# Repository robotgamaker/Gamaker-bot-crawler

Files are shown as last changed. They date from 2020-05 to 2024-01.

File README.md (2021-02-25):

# Gamaker-bot-crawler
Código arduino , STLs y app para crear un pequeño robot cuadrúpedo muy ágil, con capacidad para superar obstáculos
Hay que imprimir dos veces el archivo PARpatasPistoriusV5.stl (hasta tener dos pares de patas) y 
también hay que imprimir dos veces el archivo "ChasisFinal_GamakerBot4.stl"  .
Con los dos chasis se monta un "sandwich" sujeto por 4 tornillos de métrica 3 de 20 mm de longitud (3x20).
La bateria va entre las dos planchas y los 4 miniservos. En el piso "superior " va la electrónica.

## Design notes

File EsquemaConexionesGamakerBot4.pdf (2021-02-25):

Conexiones del GamakerBot4:

A0(14): -> Tx de placa Bluetooth (BT)

A1(15): ->Rx de placa BT

A4: -> zumbador

D2: -> servo delantero derecho (hombro derecho)

D3: -> servo delantero izdo (hombro izdo)

D4: -> servo trasero derecho (cadera derecha)

D5: -> servo trasero izquierdo (cadera izda)

D6: -> servo giratorio cabeza

D8: -> LED rojo

D9: -> LED amarillo

D10:-> LED verde

D12: -> sensor ultrasónico, pin Echo

D13: -> sensor ultrasónico, pin Trigger

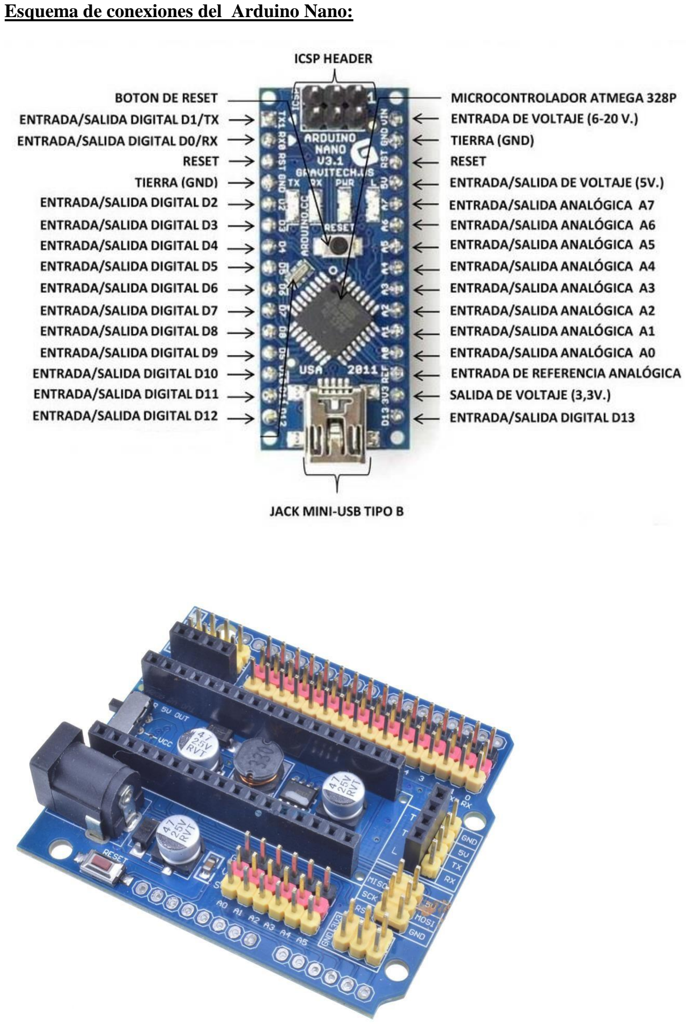
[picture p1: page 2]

Esquema de conexiones del Arduino Nano:

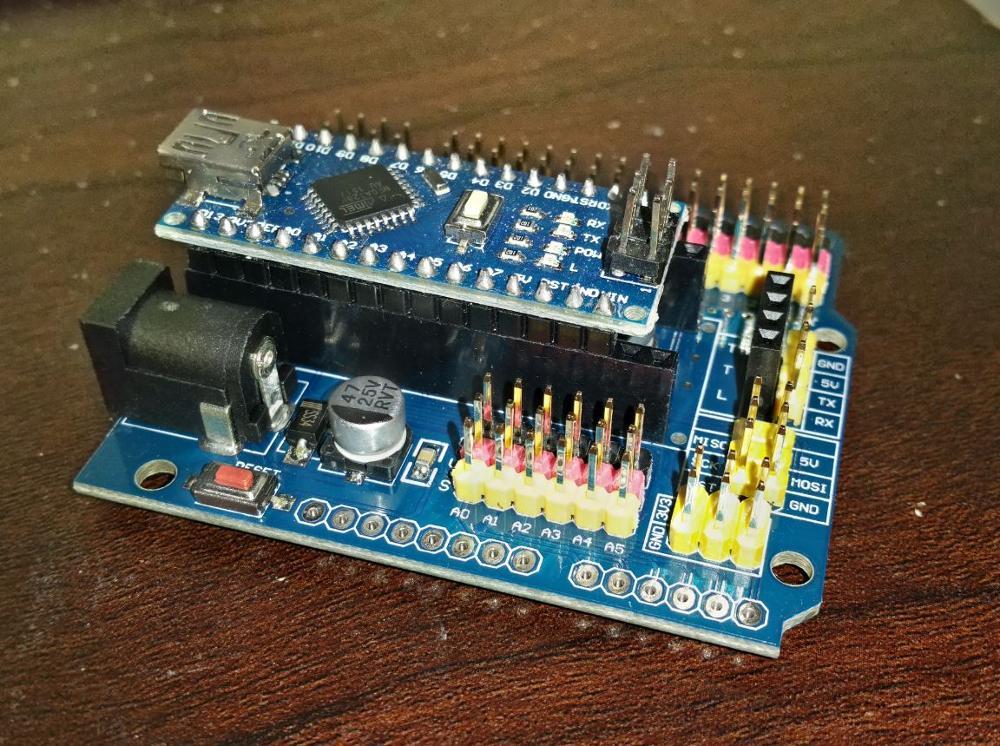
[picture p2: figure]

Distribución de teclas en la app Cheetah :

G | F | I
g | f | i
L | l | S | r | R
H | b | j
H | B | J
U | V | W
X | Y | Z

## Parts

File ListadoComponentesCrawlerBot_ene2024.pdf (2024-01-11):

Listado de componentes del robot CrawlerBot : www.3dsolid.es

Presupuesto con precios del 11/01/2024:

Miniservos (8 +2 de repuesto: 21,41€/10unids) de rotación continua (360 grados), de engranajes metálicos (los de nylon se rompen muy rápido, no comprar!): https://es.aliexpress.com/item/1005004550692203.html

Batería Lipo, 1 + repuestos, (3,7V, 1000 mA aprox ) se carga hasta 4,2 V y se conecta a GND y 5V del arduino Nano, pedir el modelo con conector blanco X5C, para luego poder recargarlo con el siguiente componente que pediremos OJO!): 7,43€:2/u

https://es.aliexpress.com/item/4001305039983.html

Cable de carga de la batería Lipo (se conecta por USB a nuestro cargador de móvil estándar: de 5V, 1A): 1,57€/unid

https://es.aliexpress.com/item/4001023158270.html

Modulos BlueTooth (slave: de 4 pines), para controlar el robot desde nuestro móvil Android con la app Cheetah (tb disponible en este gitHub) : 5,15€/2unids https://es.aliexpress.com/item/4000830084058.html

Arduino Nano: 6,98€/2 unids https://es.aliexpress.com/item/32647196840.html?spm=a2g0s.9042311.0.0.39da63c0 ATthIT (https://es.aliexpress.com/item/32647196840.html?spm=a2g0s.9042311.0.0.39da63c0ATthIT)

Tornillos de 2,5 mm de diámetro y 14 mm de largo para atornillar bien las patas al eje metálico de los servos: 2,28€/bolsa 50 unids https://es.aliexpress.com/item/32835829915.html?spm=a2g0s.9042311.0.0.3d2f63c0kaEIxs

Tornillos de 3 mm de diámetro y 20 mm de largo, para unir las dos placas de plástico del chásis : de venta en ferreterías y grandes almacenes, por ejemplo, Leroy Merlin. 2 €/bolsa

Cables de conexión de arduino de 10 cm de longitud: Hembra-hembra : 2,63 €/2 pack https://es.aliexpress.com/item/4000439969887.html

Voltímetro , para controlar el voltaje de la batería y no descargarla por debajo de los 3,7 V (se carga hasta los 4,2 V) : 2,18€/ 2 unids https://es.aliexpress.com/item/32901073658.html

Un mini-interruptor de encendido/apagado del bot: 0,97/10 unids https://es.aliexpress.com/item/4001165826718.html

- Como app de control bluetooth se puede usar la que tb se adjunta en el github (Cheetah):
https://github.com/robotgamaker/Gamaker-bot-crawler

O también “Arduino Bluetooth RC Car controller”(se aconseja tener instaladas las dos) :
https://play.google.com/store/apps/details?id=braulio.calle.bluetoothRCcontroller&hl=es_419 (https://play.google.com/store/apps/details?id=braulio.calle.bluetoothRCcontroller&hl=es_419)

-Shield para Arduino Nano: 6,56 € /2 unids https://es.aliexpress.com/item/1859164365.html

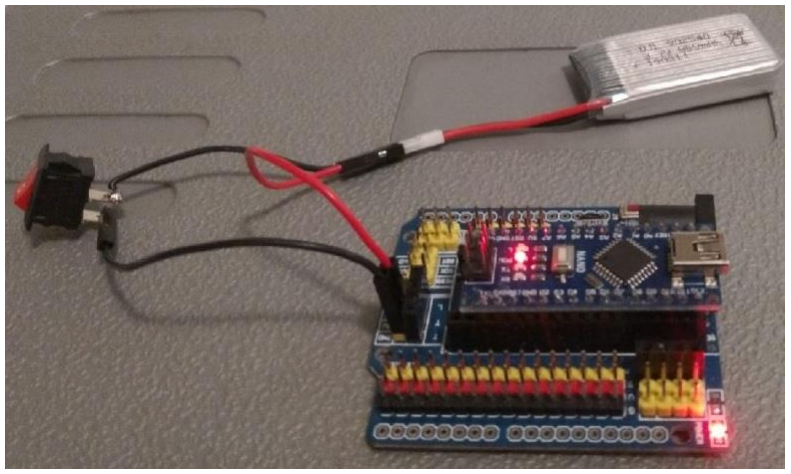
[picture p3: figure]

Link a zumbadores pasivos: 1,56€/2 unids https://es.aliexpress.com/item/32809816924.html

Link a sensor ultrasónico (detector obstáculos): 1,90€/2 unids https://es.aliexpress.com/item/4000899658467.html

Link a “semáforo led RGB” : 2,15 €/2 unids https://es.aliexpress.com/item/1005003926496876.html

1 miniservo 940D (0-180º) para girar la cabeza (8,51 €/2 unids): https://es.aliexpress.com/item/4000459542063.html

Ejemplo de presupuesto para hacer 2 crawlerBots con componentes de aliexpress:

1. 10 servos de engranaje metalico 360º(+ envio en todos) | 21,41€
2. 2 baterias Lipo 3,7 V, 1000 mA : | 7,50
3. 4 cables de carga de de batería (2 por robot) : | 6,15
4. 2 modulos Bluetooth hc-06 (4 pins) : | 4,68
5. 2 placas controladoras Arduino nano con cable: | 6,98
6. 1 bolsas de tornillos 2,5 x 14 mm: | 2,54
7. 1 bolsas de tornillos 3 x 20 mm en Leroy Merlin: | 2
8. 2 bolsitas de cables female-female: | 2,63
9. 2 minivoltimetros para controlar el voltaje de la batería: | 2,18
10. Kit de 10 mininteruptores: | 0,97
11. 2 shields para conectar el nano, la alimentación y los motores 6,56
12. 2 zumbadores pasivos (para que emita sonido/melodías) | 1,56
13. 2 sensores ultrasónicos (detectores de obstáculos): | 1,90
14. 2 semaforos leds , Rojo, Verde, Amarillo | 2,15
15. 2 miniservos 0-180º MG90D : | 8,51
16. 2 Cajas grande (bazar) de plástico transp para guardar todo....... 5
TOTAL: | 82,72
Cada pareja de crawlerBot costaría 82,72/2= 41,36 aprox (los precios pueden variar)
*Precios del 11/01/2024

By Marcos Sánchez

Contacto : markrehab@hotmail.com

https://youtu.be/afSSLWHGoCMhttps://youtu.be/Y1tGxN8LFB4

http://www.3dsolid.es

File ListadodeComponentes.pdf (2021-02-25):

Listado de componentes del robot Gamaker-bot 4 Crawler :

Miniservos (4 + repuestos) de rotación continua (360 grados), de engranajes metálicos (los de nylon se rompen muy rápido, no comprar!): https://es.aliexpress.com/item/32950372601.html?spm=a2g0o.cart.0.0.57dc3c00khVMC8&mp=1 (https://es.aliexpress.com/item/32950372601.html?spm=a2g0o.cart.0.0.57dc3c00khVMC8&mp=1)

Un miniservo estándar 0-180º:

https://es.aliexpress.com/item/4000933394404.html?spm=a2g0o.cart.0.0.259b3c00zS4MK5&mp=1

Batería Lipo, 1 + repuestos, (3,7V, 1000 mA aprox ) se carga hasta 4,2 V y se conecta a GND y 5V del arduino Nano, pedir el modelo con conector blanco X5C, para luego poder recargarlo con el siguiente componente que pediremos OJO!):

https://es.aliexpress.com/item/4001127625537.html?spm=a2g0s.9042311.0.0.274263c0nBTT 4L (https://es.aliexpress.com/item/4001127625537.html?spm=a2g0s.9042311.0.0.274263c0nBTT4L)

Cable de carga de la batería Lipo (se conecta por USB a nuestro cargador de móvil estándar: de 5V, 1A):

https://es.aliexpress.com/item/32969002546.html?spm=a2g0s.9042311.0.0.677063c0Q2Q8M b (https://es.aliexpress.com/item/32969002546.html?spm=a2g0s.9042311.0.0.677063c0Q2Q8Mb)

Modulos BlueTooth (slave: de 4 pines), para controlar el robot desde nuestro móvil Android con la app Cheetah (tb disponible en este gitHub) : https://es.aliexpress.com/item/32632724017.html?spm=a2g0o.cart.0.0.11ad3c00Q6e6XO&mp=1 (https://es.aliexpress.com/item/32632724017.html?spm=a2g0o.cart.0.0.11ad3c00Q6e6XO&mp=1)

Arduino Nano:
https://es.aliexpress.com/item/32647196840.html?spm=a2g0s.9042311.0.0.39da63c0 ATthIT (https://es.aliexpress.com/item/32647196840.html?spm=a2g0s.9042311.0.0.39da63c0ATthIT)

Tornillos de 2,5 mm de diámetro y 14 mm de largo para atornillar bien las patas al eje metálico de los servos:
https://es.aliexpress.com/item/32835829915.html?spm=a2g0s.9042311.0.0.3d2f63c0kaEIxs

Tornillos de 3 mm de diámetro y 20 mm de largo, para unir las dos placas de plástico del chásis : de venta en ferreterías y grandes almacenes, por ejemplo, Leroy Merlin.

Cables de conexión de arduino de 10 cm de longitud: Macho-Hembra, y hembra-hembra :

https://es.aliexpress.com/item/4000439969887.html?spm=a2g0s.9042311.0.0.274263c0t1IvQ W (https://es.aliexpress.com/item/4000439969887.html?spm=a2g0s.9042311.0.0.274263c0t1IvQW)

Voltímetro , para controlar el voltaje de la batería y no descargarla por debajo de los 3,7 V (se carga hasta los 4,2 V) : https://es.aliexpress.com/item/32825671226.html?spm=a2g0s.9042311.0.0.274263c0WNp1 M5 (https://es.aliexpress.com/item/32825671226.html?spm=a2g0s.9042311.0.0.274263c0WNp1M5)

Un mini-interruptor de encendido/apagado del bot: https://es.aliexpress.com/item/32832762868.html?spm=a2g0o.cart.0.0.e6c13c00k5ehAD&mp=1

- Como app de control bluetooth se puede usar la que tb se adjunta en el github (Cheetah)
O también “Arduino Bluetooth RC Car controller”: https://play.google.com/store/apps/details?id=braulio.calle.bluetoothRCcontroller&hl=es_419 (https://play.google.com/store/apps/details?id=braulio.calle.bluetoothRCcontroller&hl=es_419)
- La placa de conexiones de alimentación la haremos manualmente con el soldador y un trocito rectángular de PCB.

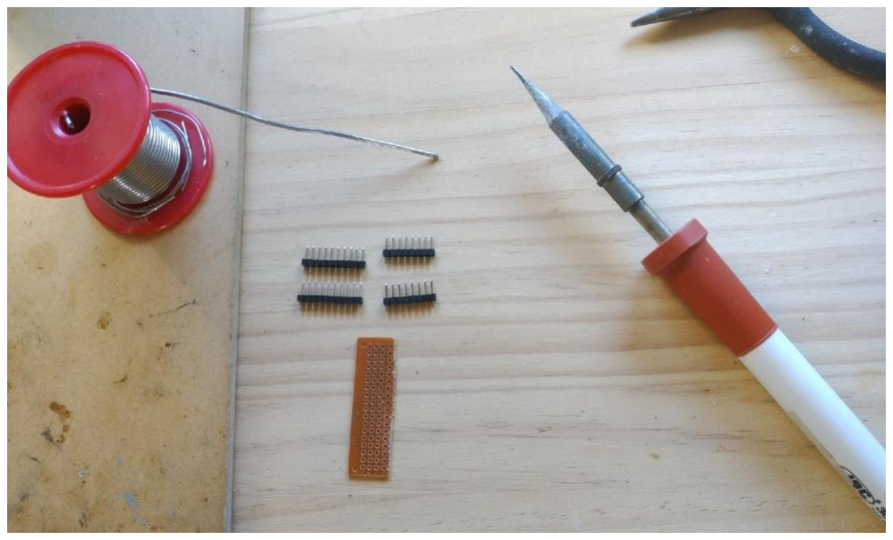
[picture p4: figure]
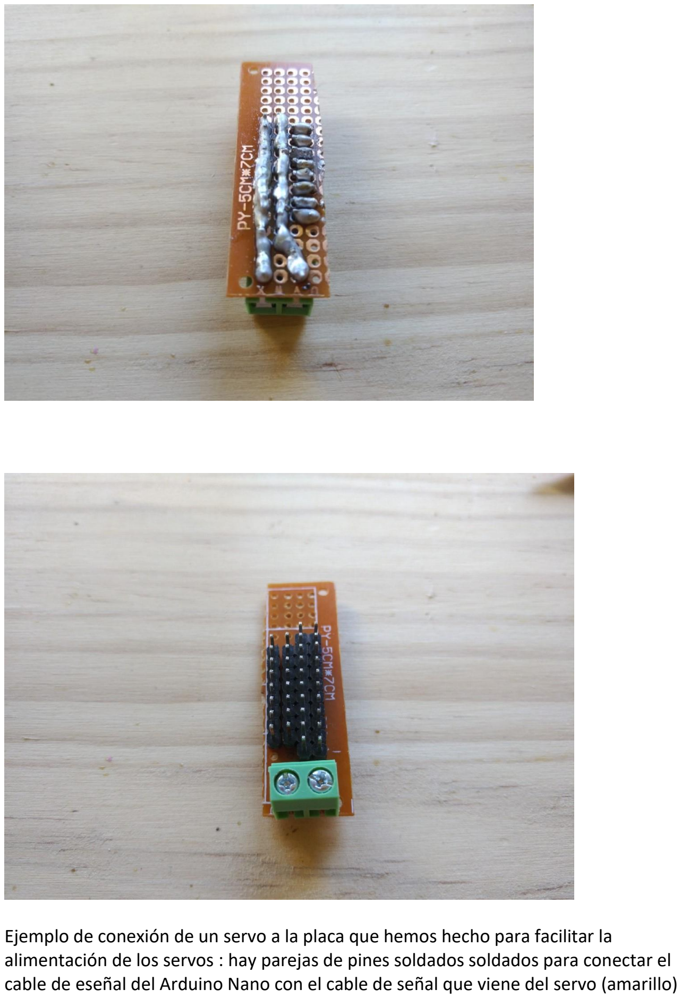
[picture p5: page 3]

Ejemplo de conexión de un servo a la placa que hemos hecho para facilitar la alimentación de los servos : hay parejas de pines soldados soldados para conectar el cable de eseñal del Arduino Nano con el cable de señal que viene del servo (amarillo)

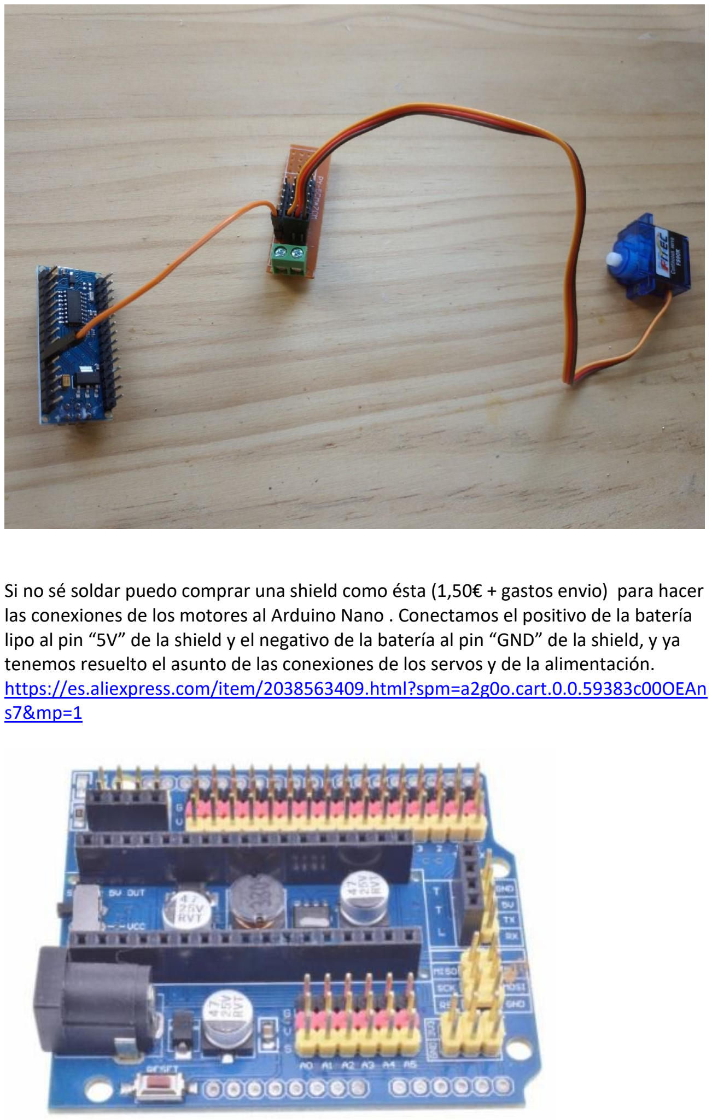
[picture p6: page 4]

Si no sé soldar puedo comprar una shield como ésta (1,50€ + gastos envio) para hacer las conexiones de los motores al Arduino Nano . Conectamos el positivo de la batería lipo al pin “5V” de la shield y el negativo de la batería al pin “GND” de la shield, y ya tenemos resuelto el asunto de las conexiones de los servos y de la alimentación. https://es.aliexpress.com/item/2038563409.html?spm=a2g0o.cart.0.0.59383c00OEAns7&mp=1 (https://es.aliexpress.com/item/2038563409.html?spm=a2g0o.cart.0.0.59383c00OEAns7&mp=1)

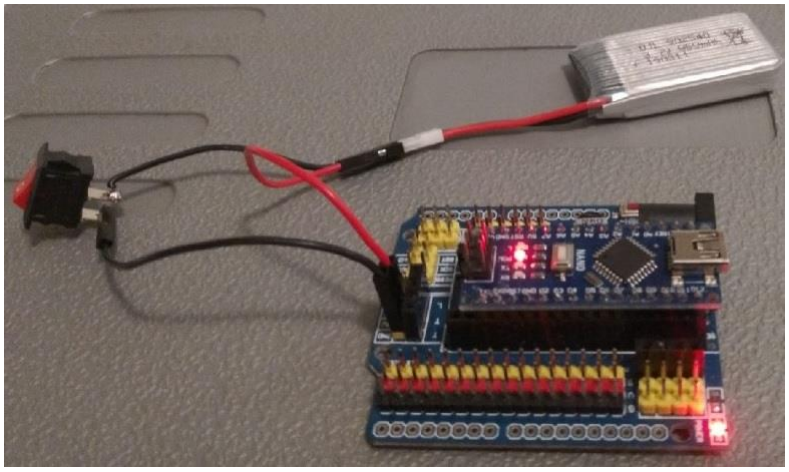
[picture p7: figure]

Ejemplo de presupuesto para hacer 2 gamakerBots4 con componentes de aliexpress:
1. 10 servos de engranaje metalico (+ envio en todos) | 14,37 €
2. 2 miniservos MG-90D (0-180º) | 5,57
3. 2 baterias Lipo 3,7 V, 1000 mA : | 6,55
4. 4 cables de carga de de batería (2 por robot) : | 2,56
5. 2 modulos Bluetooth hc-06 (4 pins) : | 5,12
6. 2 placas controladoras Arduino nano con cable: | 4,48
7. 2 bolsas de tornillos 2,5 x 14 mm: | 3,12
8. 2 bolsas de tornillos 3 x 20 mm en Leroy Merlin: | 3,40
9. 2 bolsitas de cables male-female, y 2 female-female: | 3,08
10. 2 minivoltimetros para controlar el voltaje de la batería: | 3,10
11. Kit de 10 mininterruptores: | 1,22
12. 2 shields para conectar el nano, la alimentación y los motores 4,83
13. 2 zumbadores pasivos (para que emita sonido/melodías) | 1,11
14. 2 sensores ultrasónicos (detectores de obstáculos): | 2,31
TOTAL: | 60,82
Cada gamakerbot4, costaría 55,25/2= 30,41€

Link a zumbadores pasivos: https://es.aliexpress.com/item/32809816924.html?spm=a2g0o.cart.0.0.248c3c00KwZT1z&mp=1 (https://es.aliexpress.com/item/32809816924.html?spm=a2g0o.cart.0.0.248c3c00KwZT1z&mp=1)

Link a sensor ultrasónico (detector obstáculos): https://es.aliexpress.com/item/4000899658467.html?spm=a2g0o.cart.0.0.34bf3c00Ut3WMY&mp=1

By Marcos Sánchez . Gamaker (Asociación de makers de Vitoria-Gasteiz) 21 mayo del 2020

Contacto : markrehab@hotmail.com

https://youtu.be/afSSLWHGoCMhttps://youtu.be/Y1tGxN8LFB4

http://www.3dsolid.es

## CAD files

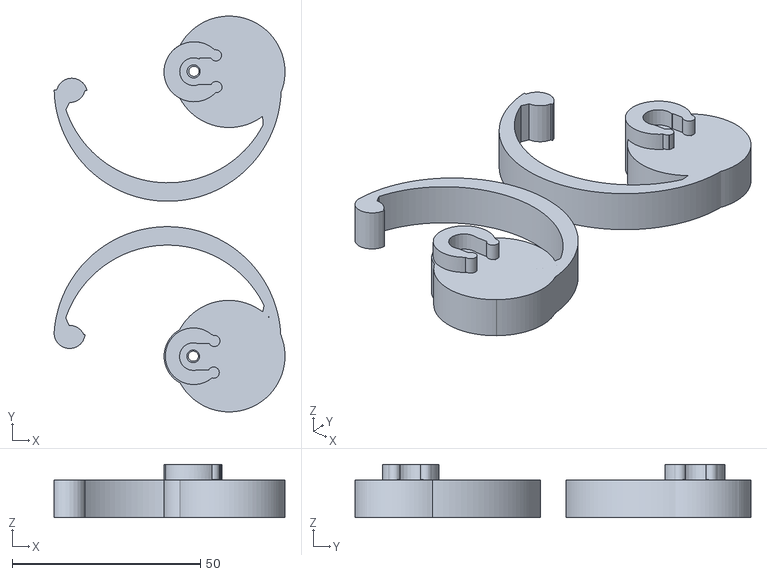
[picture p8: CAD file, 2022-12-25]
parPatasPistorius2022.stl
61.4 x 105.2 x 14.2

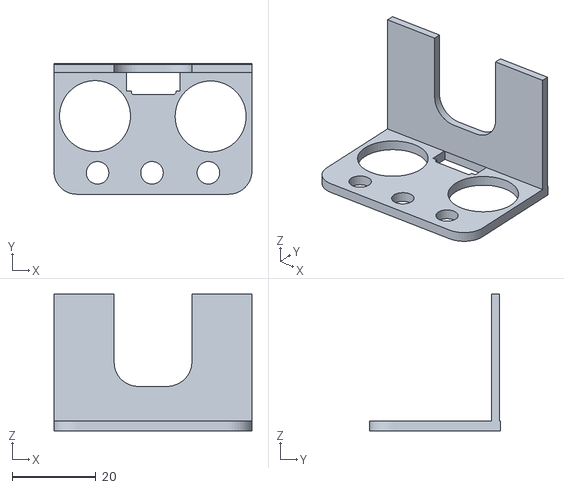
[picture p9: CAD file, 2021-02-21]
Cabeza_SensorUS.stl
47.3 x 31.2 x 32.7

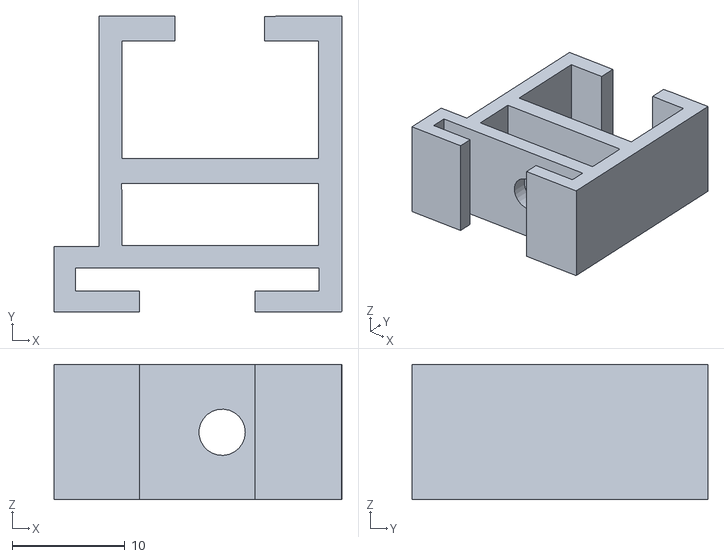
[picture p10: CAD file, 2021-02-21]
SoporteTarjetas.stl
25.5 x 26.3 x 12.0

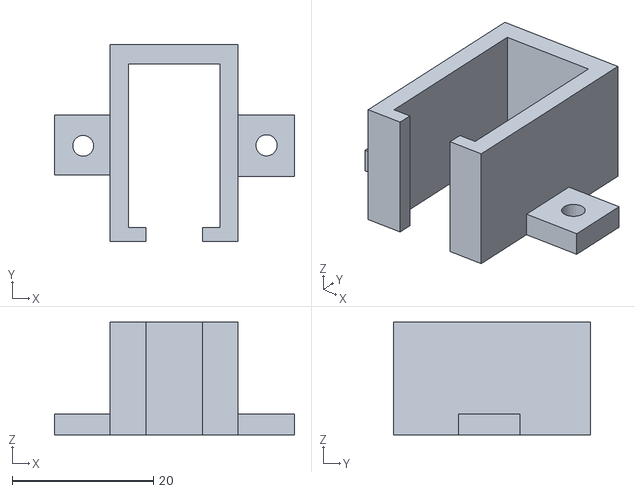
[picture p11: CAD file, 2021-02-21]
SoporteServoCabeza.stl
34.0 x 28.0 x 16.0

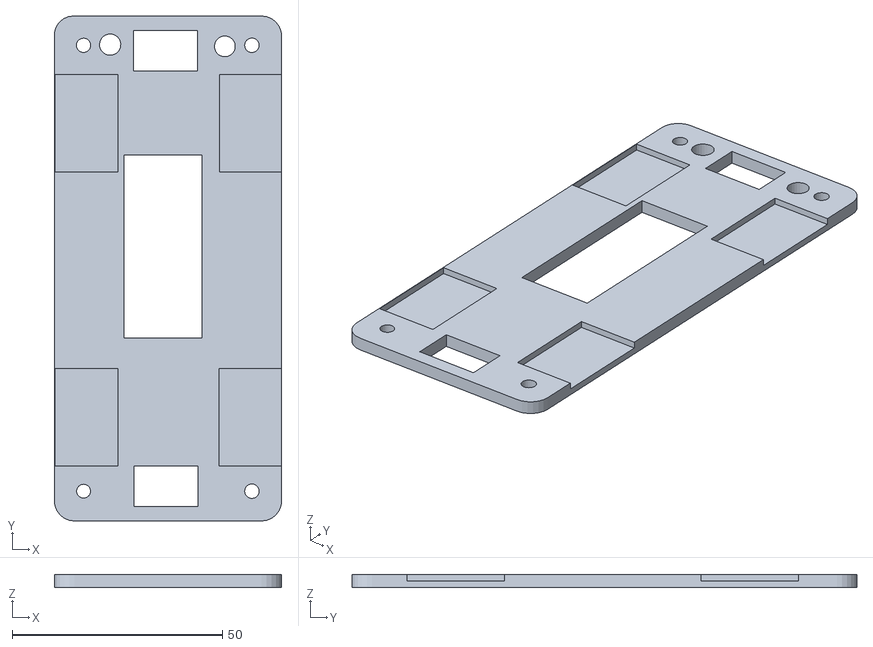
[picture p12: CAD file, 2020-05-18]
ChasisFinal_GamakerBot4.stl
54.1 x 120.0 x 3.00

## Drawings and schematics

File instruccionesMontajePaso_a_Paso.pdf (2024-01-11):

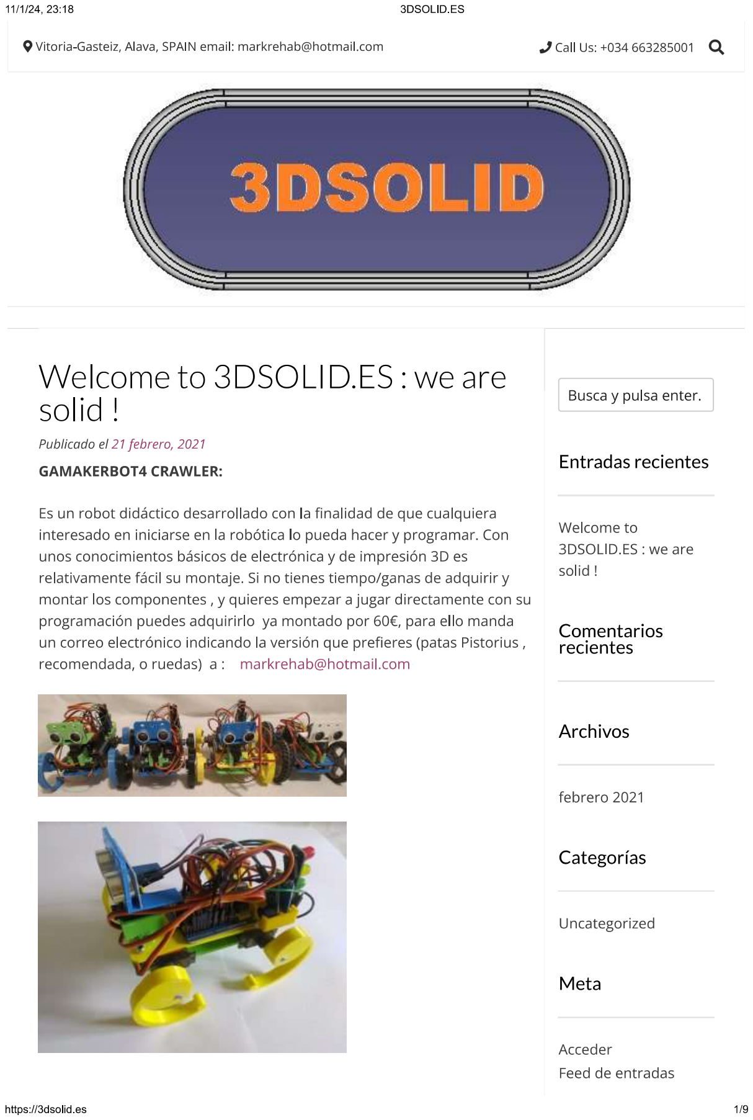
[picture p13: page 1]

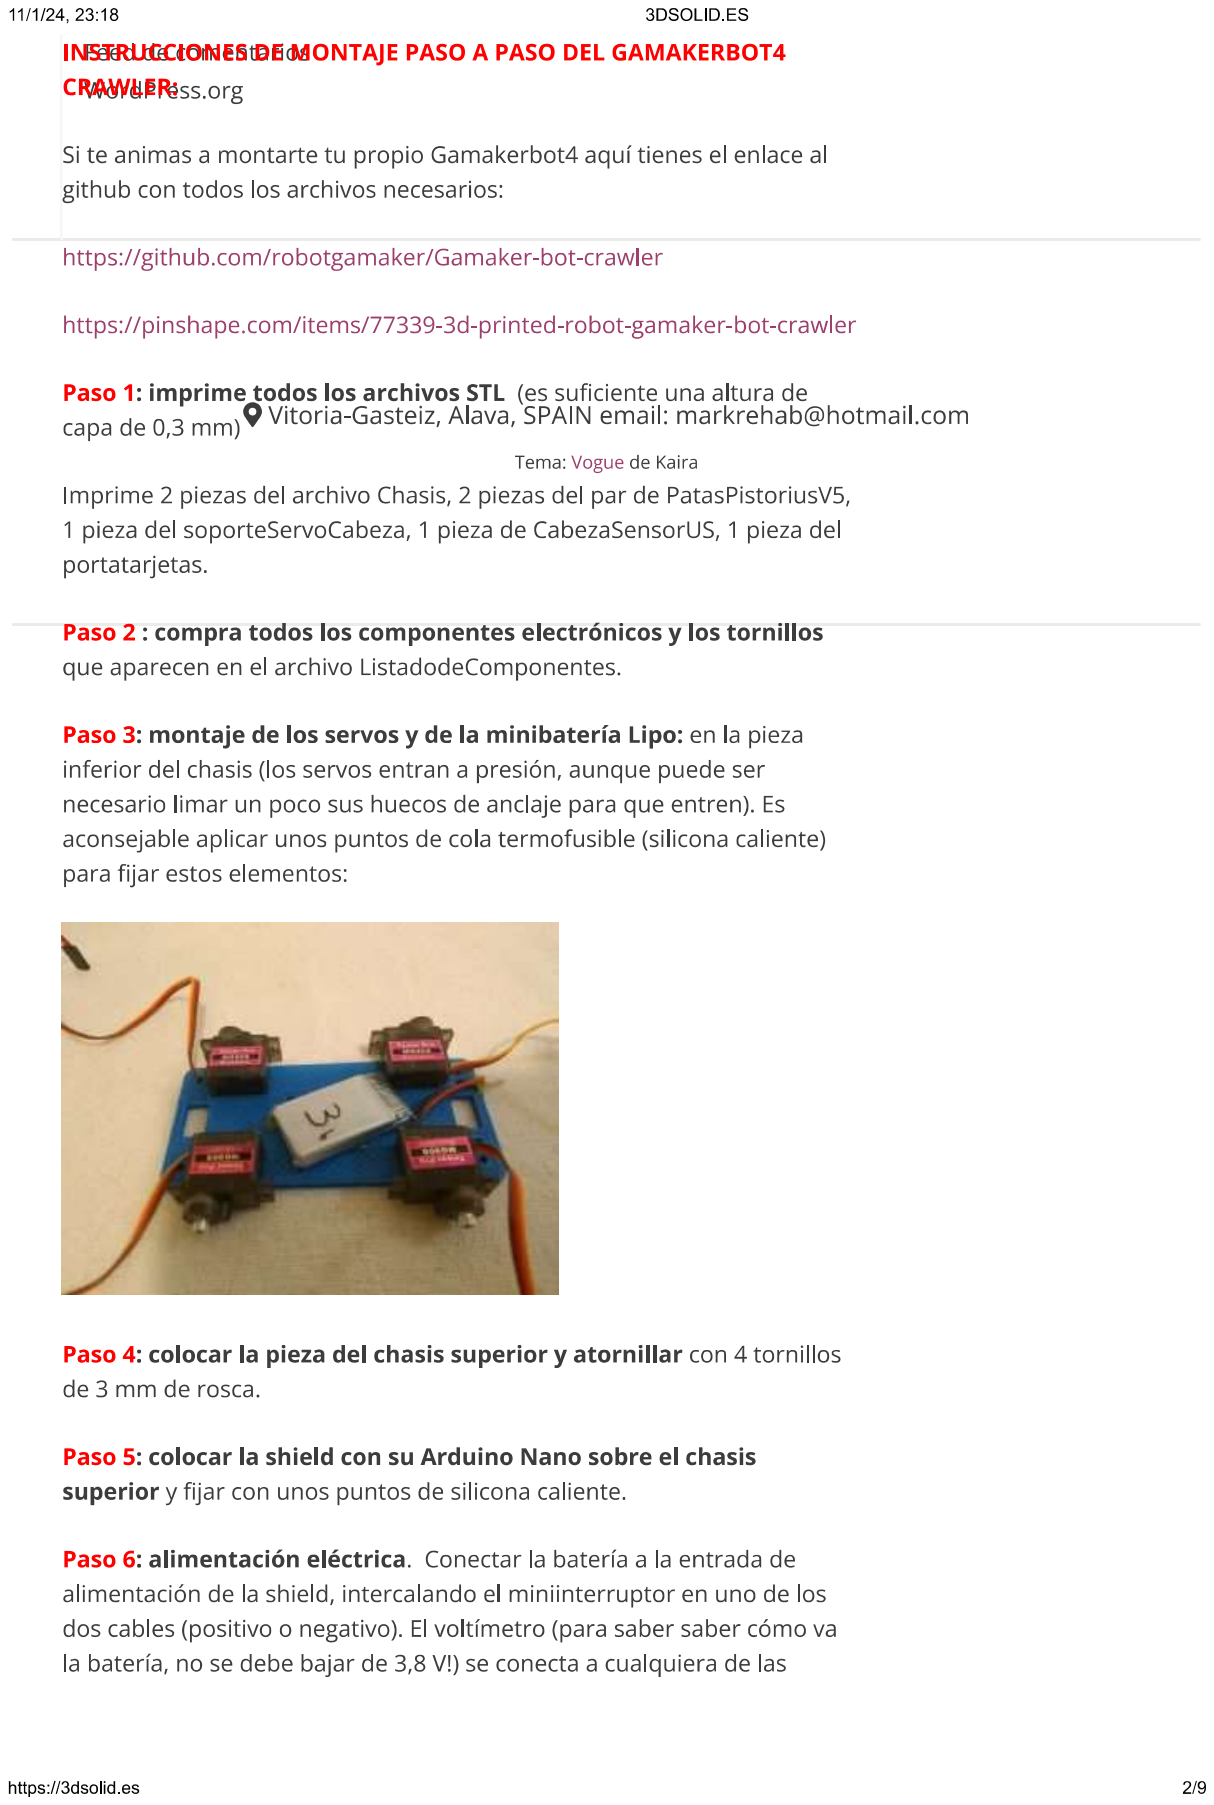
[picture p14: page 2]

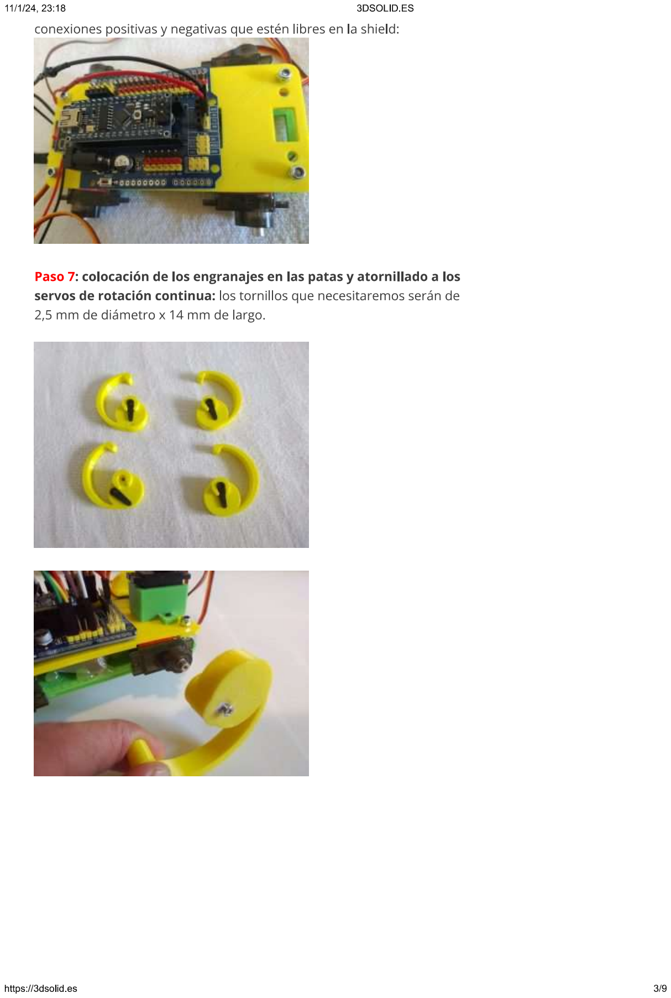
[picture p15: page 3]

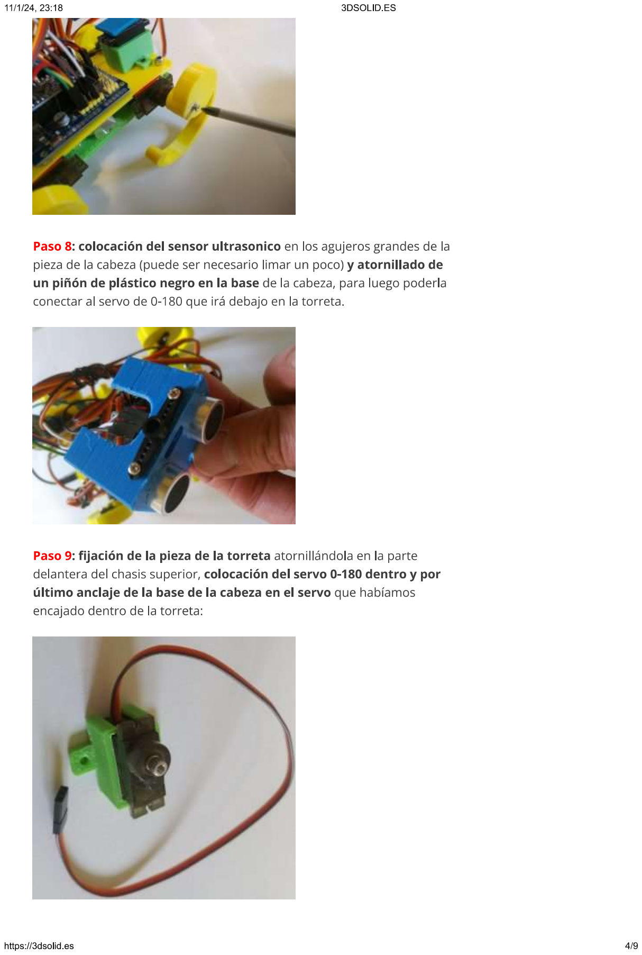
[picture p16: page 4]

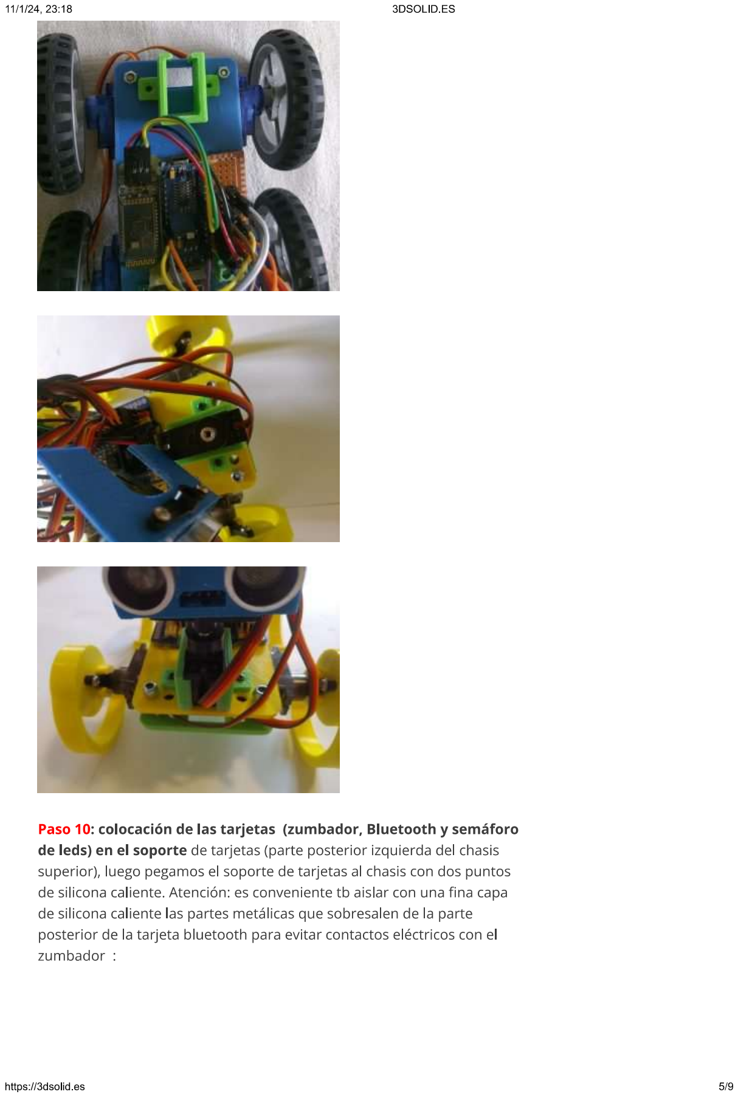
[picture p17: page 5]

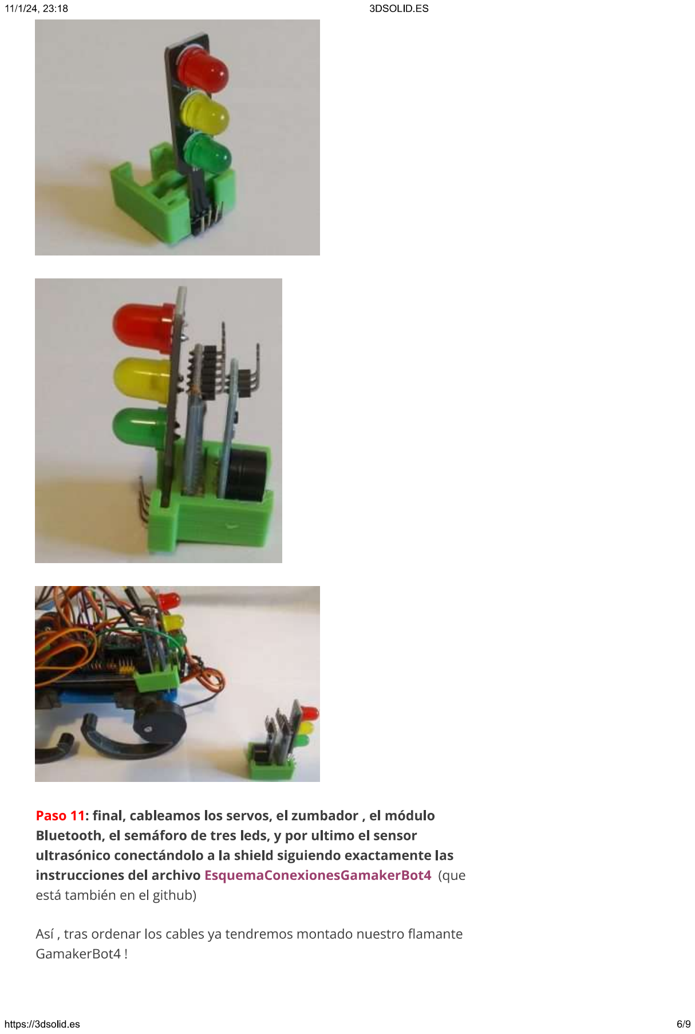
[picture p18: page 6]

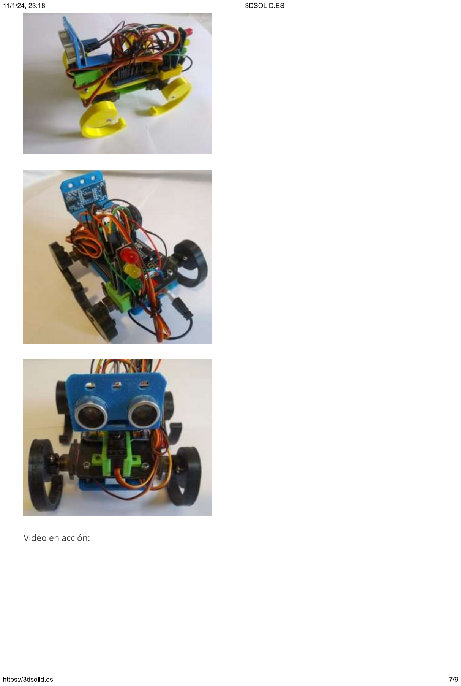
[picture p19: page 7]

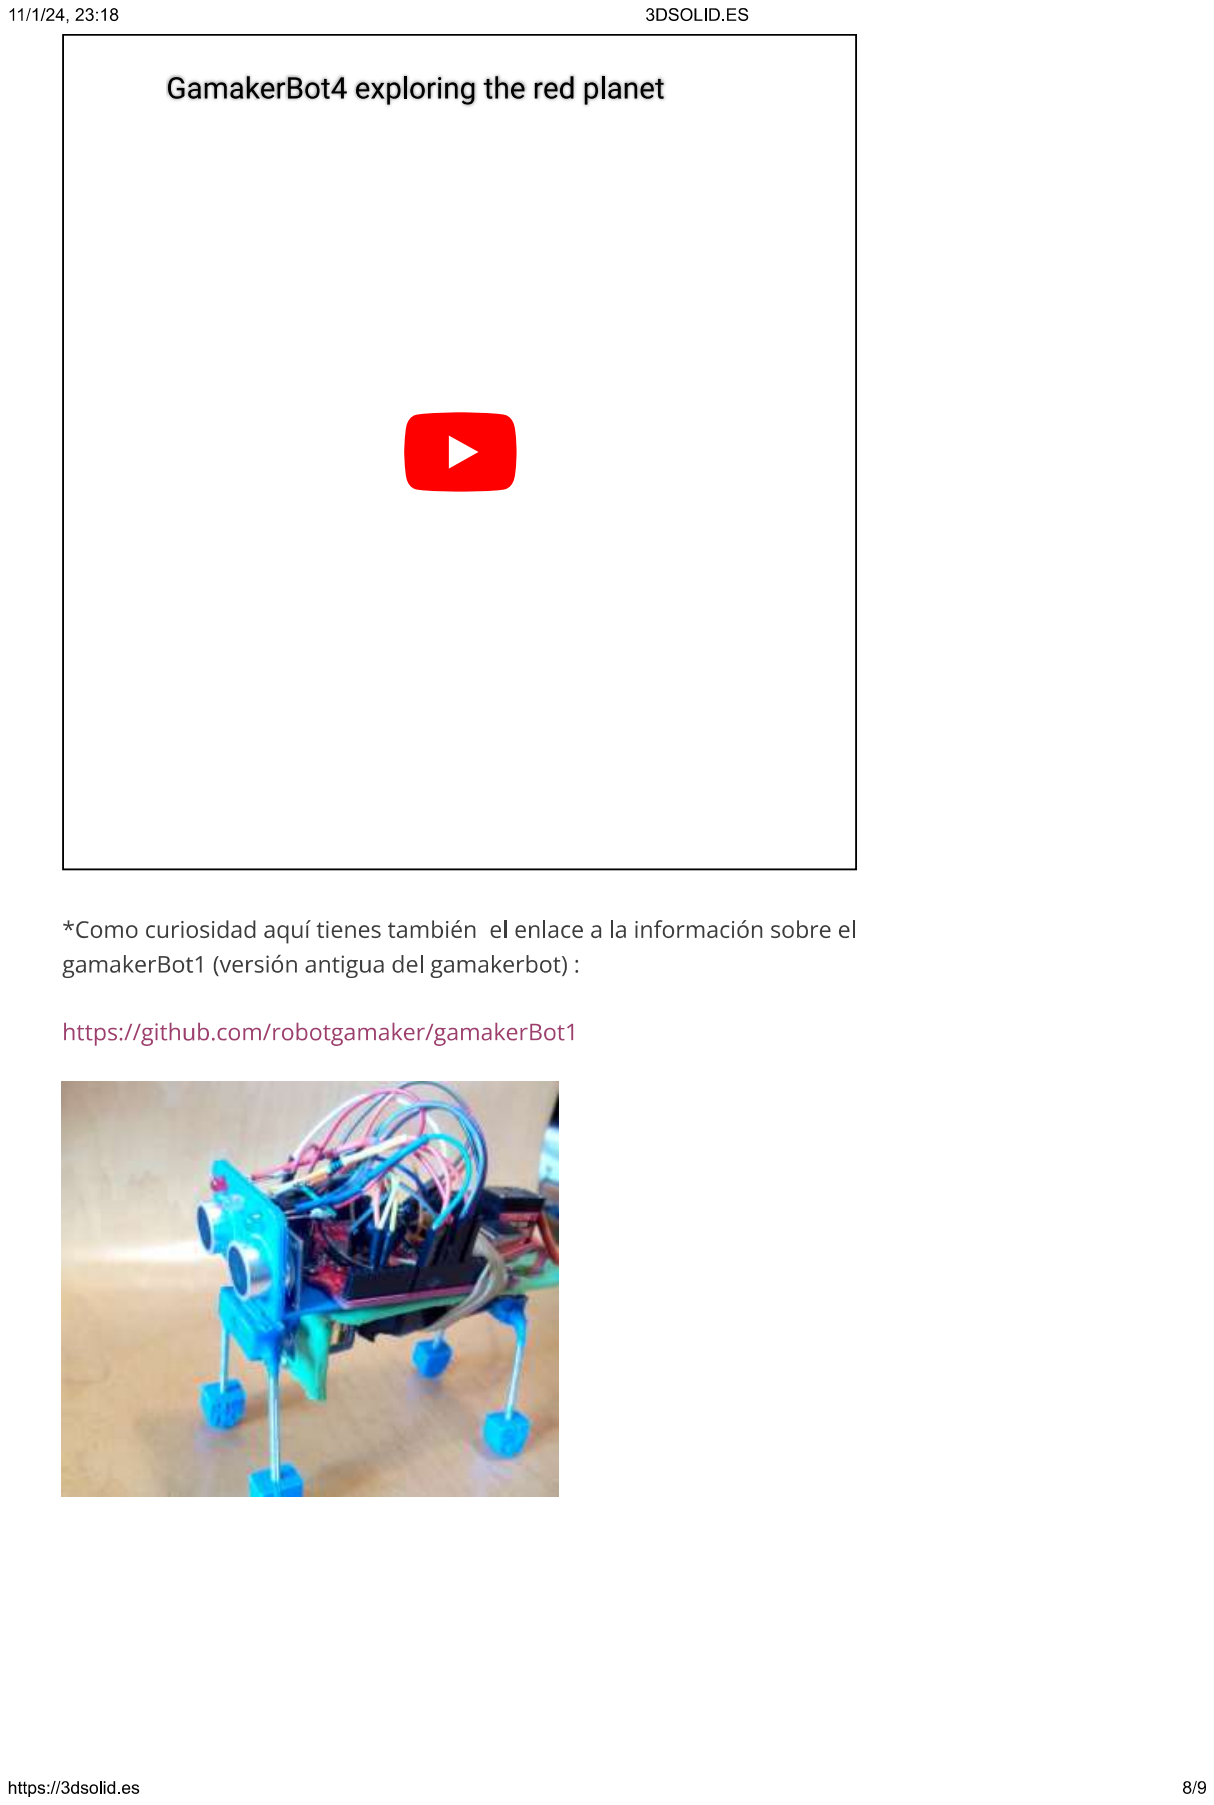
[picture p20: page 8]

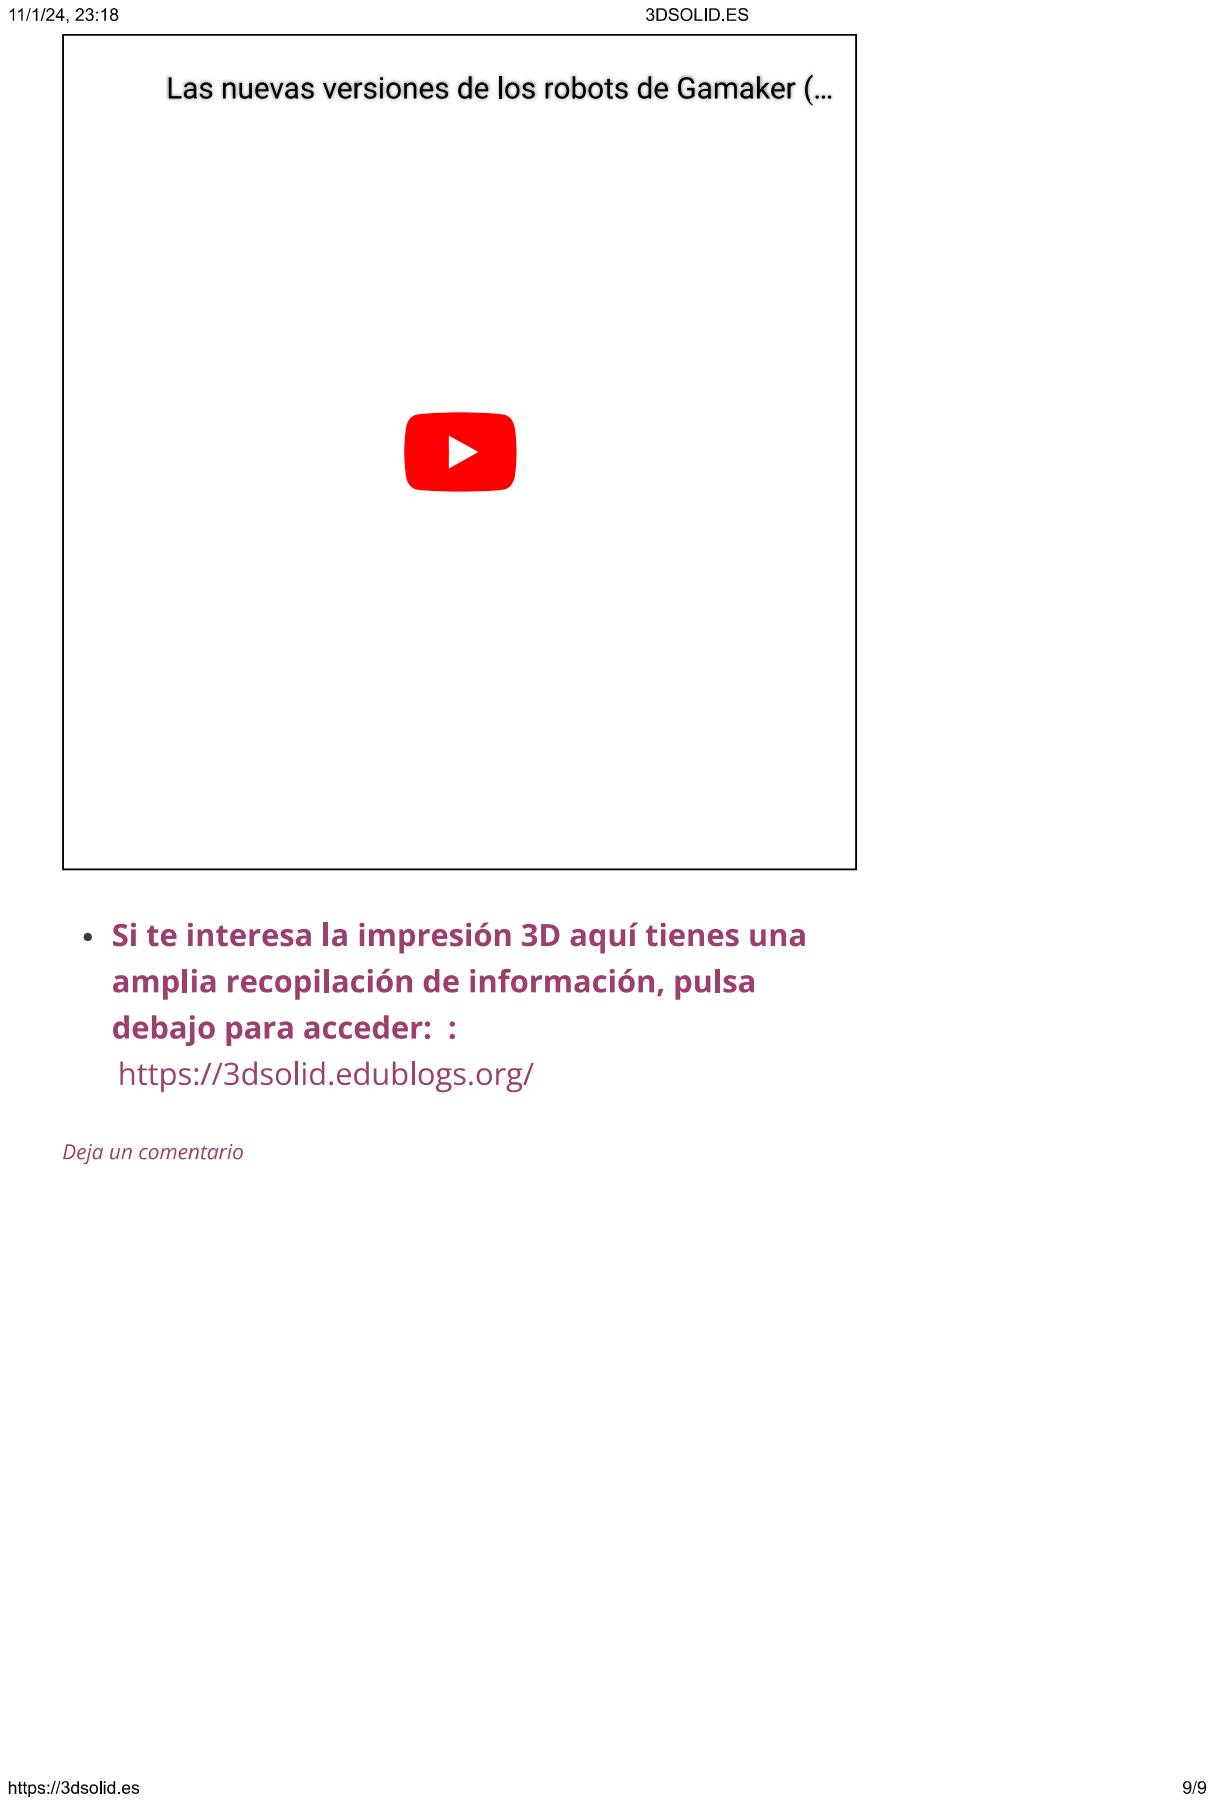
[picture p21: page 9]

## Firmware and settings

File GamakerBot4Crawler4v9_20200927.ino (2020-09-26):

                                                                                     /*
  Cheetah 4.0 by
  Marcos Sanchez
     http://www.3dsolid.es
      & 
  
  Mr Q
    http://www.god-i.com
 

 * 
 */

// include the servo library
#include <Servo.h>
#include <SoftwareSerial.h>// import the serial library
SoftwareSerial Genotronex(A1,A2); // RX-> A2   ;  TX -> A1
const int pinBuzzer = A3;  // pin for buzzer(zumbador), posible incorporación futura
int lightningPin = A5;  //posible arma a incorporar en el futuro
int ledpin = A4; // led on A4
int BluetoothData; // the data given from the app smartphone

Servo BL1;  // create a servo object:  Cadera trasera izda


Servo BR1;  // create a servo object:  Cadera trasera izda


Servo FL1;  // create a servo object:  Hombro delantero izdo


Servo FR1;  // create a servo object:  Hombro delantero dcho


  
int d;  // delay corto
int dMedium; // delay mediano
int dLong;   //delay largo
int dPruebas;  //delay pruebas
int i;
int first;  // variable que se usara como booleana (0 o 1) para indicar si es la primera conexion BT

//  variables que cambiaran de valor con el tiempo/delays
long previousMillis = 0;  
unsigned long currentMillis = 0;

void setup() {

  pinMode(ledpin, OUTPUT);
  pinMode(pinBuzzer, OUTPUT);
  pinMode(lightningPin, OUTPUT);
  
  FR1.attach(2); // HOMBRO DCHO , se conecta al pin D2 del Arduino
  delay(dMedium);
  
  FL1.attach(3); // HOMBRO IZDO, se conecta al pin D3 del Arduino
  delay(dMedium);
   
  BR1.attach(4); // CADERA DCHA, se conecta al pin D4 del Arduino
  delay(dMedium);

  BL1.attach(5);  //CADERA IZDA, se conecta al pin D5 del Arduino
  delay(dMedium);   



 d=20;      ////delay corto
 dMedium = 100;
 dLong = 300;
 
 first=0;   // variable para recoger la primera conexion BlueTooth

dPruebas=300;    ///////////////////////////////////////////delay PRUEBAS

previousMillis = 0;  //  las variables de tiempo/retraso se inicializan a 0
currentMillis = 0;   //  las variables de tiempo/retraso se inicializan a 0

 
Genotronex.begin(9600);
Genotronex.flush();
 delay(100);

////   Wait in SETUP for first BT transmission    /////

while(!Genotronex.available())

{/*do nothing*/   }
  BluetoothData = Genotronex.read();
  delay(50);
//  full_Stop();
//delay(100);

   
}   ///// END SETUP



                              ////////////////////////////////////////////////////////////////////            ///////////////////////////////////////////////////////////////////
void loop() {                             //////////////////////////////// LOOP   ///////////////////  LOOP   ////////////////// LOOP ///////////////////////////////////////


     //  Pruebas iniciales antes de usar el control BT
     //full_Stop ();   //parada de todas las ruedas
     //delay(20);
     //wheelsForward () ;
    // delay(20);
    // wheelsRight ();
     //delay(20);
    // wheelsBack () ;
     //delay(20);


       //////////////////////////////////////////////////CODIGO DE CONTROL DE BLUETOOTH   ///////////////////////////////////////////////////////////////
while(Genotronex.available())
{
  //delay(30);
  
    if ((BluetoothData=='F')&&(first==1)){  // ADELANTE , a partir de la segunda lectura BT/// CON MARCHA DE ruedas  (en la primera lectura BT first pasa a ser 1; Se inicia a 0)
      //Genotronex.println(BluetoothData);
      //Genotronex.println("Bluetooth ON ! ");
        full_Stop();
        delay(d);
        wheelsForward () ;
        delay(200);
  }  // cierre if


  if ((BluetoothData=='f')&&(first==1)){                     // ADELANTE  ;  se filtra la primera orden BT que suele ser erronea
      //Serial.print(BluetoothData);
      //Genotronex.println("Bluetooth ON ! ");
      full_Stop();
      delay(d);
      wheelsForward () ;
      delay(100);     
     }


    if ((BluetoothData=='b')&&(first==1)){   //MARCHA ATRAS  300 ms
      full_Stop();
      delay(d);
      wheelsBack() ;
      delay(200);
  }  // cierre if

    if (((BluetoothData=='B'))&&(first==1)){    //MARCHA ATRAS durante 300 ms= 1segundo
      full_Stop();
      delay(d);
      wheelsBack () ;
      delay(300);
     }
   
    if (BluetoothData=='S'){    //  (señal de triangulo en app )  // Parada en posicion Base, posición felina
      full_Stop();
      delay(d);
     }

    if (BluetoothData=='X'){    //  (señal de triangulo en app )
      full_Stop();
      delay(d);
     }


    if ((BluetoothData=='i')&&(first==1)){    // adelante y a la derecha , primera flecha diagonal
        full_Stop();
        delay(d);
       wheelsRightSlow();
       delay(20);
       wheelsForward () ;
       delay(100); 
    }

    if ((BluetoothData=='I')&&(first==1)){    // adelante y a la dcha, segunda flecha diagonal
        full_Stop();
        delay(d);
       wheelsRight();
       delay(100);
       wheelsForward () ;
       delay(100); 
     }



    if((BluetoothData=='l')&&(first==1)){      ////// , GIRO LENTO IZDA
        full_Stop();
        delay(d);
       wheelsLeftSlow();
       //delay(20);   
     }


     if ((BluetoothData=='L')&&(first==1)){    //  (señal de triangulo en app )  giro a la izda
        full_Stop();
        delay(d);
       wheelsLeft();
       //delay(20);
       wheelsForward () ;
        //delay(200);
     }

      if ((BluetoothData=='r')&&(first==1)){        /////Giro a la DCHA
        full_Stop();
        delay(d);
       wheelsRightSlow();
       //delay(20);
     }


       if ((BluetoothData=='R')&&(first==1)){    //  (señal de triangulo en app ) //giro a la DCHA
        full_Stop();
        delay(d);
       wheelsRight();
       //delay(100);

     }
 

    if (((BluetoothData=='G')&&(first==1))){    //adelante y a la izda;  se filtra la primera orden BT que suele ser erronea
        full_Stop();
        delay(d);
       wheelsLeft();
       delay(20);
       wheelsForward () ;
       delay(100); 
     }

    if ((BluetoothData=='g')&&(first==1)){    //adelante y a la izda, girando en el sitio sobre sí mismo;  se filtra la primera orden BT que suele ser erronea
        full_Stop();
        delay(d);
       wheelsLeftSlow();
       delay(20);
       wheelsForward () ;
       delay(100); 
     }



   if (((BluetoothData=='J')&&(first==1))){
      //right_Back(30); 
      delay(300);       
   
     }

   if (((BluetoothData=='j')&&(first==1))){     
      //full_backRightTurn(20); 
      delay(300);     
     }


     
     
   if ((BluetoothData=='H')&&(first==1)){  
      //left_Back(30); 
      delay(300);     
  
     }

   if ((BluetoothData=='h')&&(first==1)){      
      //full_backLeftTurn(20); 
      delay(dLong);  
     }

     
    if ((BluetoothData=='W')||(BluetoothData=='w')){     //Front lights ON 
      wheelsForward () ;
      delay(300);
     // horizontal(70);    //  marcha tumbado con ruedas
      //delay(500);
     }



       if (BluetoothData=='v'){    ////HORN ON  claxon   vuelta a posicion estndar Boston
      full_Stop();
      delay(d);
     }


     if ((BluetoothData=='F')&&(first==0)){                     // primera señal de Bluetooth: `F` ADELANTE--->>> ignorarlo! 


     full_Stop();
      delay(d);
     }    
     
      first =1;    // Inicializa la variable first para empezar a recoger órdenes
      //delay(100);  

BluetoothData= Genotronex.read();   //al final recoge/lee de nuevo el mensaje Bluetooth
delay(100);


     
  } //cierre del:     while(Genotronex.available());   


    


 
}  ////////////////////////////////////////////// cierre del LOOP   ////////////////////////////////////////////////////////////////////


     ////////////////////////END LOOP////////////////////////////////////END  LOOP //////////////////////////////////////////////////////






//////////Funcion parar todas las ruedas del robot Crawl
void full_Stop()
{
  FR1.write(90);     // STOP wheel
    FL1.write(90);     // STOP wheel
      BR1.write(90);     // STOP wheel
        BL1.write(90);     // STOP wheel
}



     

int retraso(int r)       //////////////////////////////////////   FUNCION RETRASO para sustituir a la llamada a delay(r)     /////////////////////////////////////////////////////////////
{
  currentMillis = millis();    // Se toma el tiempo actual
  if (currentMillis - previousMillis > r){

// Si se cumple la condicion se guarda el nuevo tiempo
previousMillis = currentMillis;
return 1;
  }
  else return 0;
}





 void zumbido1()
 {
  //generar tono de 440Hz durante 1000 ms
  tone(pinBuzzer, 440);
  delay(1000);
 
  //detener tono durante 500ms  
  noTone(pinBuzzer);
  delay(500);
 
  //generar tono de 523Hz durante 500ms, y detenerlo durante 500ms.
  tone(pinBuzzer, 523, 300);
  delay(500);
}



 void zumbido2()
 {
  //detener tono durante 500ms  
  noTone(pinBuzzer);
  delay(500);
 
  //generar tono de 523Hz durante 500ms, y detenerlo durante 500ms.
  tone(pinBuzzer, 523, 300);
  delay(500);
}



 

void wheelsForward ()      ///////
{
int pos1 = 10;    // variable to store the servo position    HOMBRO DCHO   FR1
int pos2 = 170;    // variable to store the servo position   HOMBRO IZDO    FL1
int pos3 = 10;    // variable to store the servo position    CADERA DCHA    BR1
int pos4 = 170;    // variable to store the servo position   CADERA IZDA    BL1
  
 FR1.write(pos1); 
 BR1.write(pos3); 
  while((currentMillis - previousMillis) < dPruebas)    //  dPruebas=interval=delay=retraso     ////    OJO  :: este While equivale a delay(dPruebas);
  { 
     currentMillis = millis();    // Se toma el tiempo actual
     
    //check sensors and respond if necessary 
  }
FL1.write(pos2);
BL1.write(pos4);

  previousMillis = currentMillis;
  currentMillis = millis();    // Se toma el tiempo actual


     while((currentMillis - previousMillis) < dPruebas)    //  dPruebas=interval=delay=retraso      ////    OJO  :: este While equivale a delay(dPruebas);
    { 
        currentMillis = millis();    // Se toma el tiempo actual
        
        //check sensors and respond if necessary 
    }
  previousMillis = currentMillis;
  currentMillis = millis();    // Se toma el tiempo actual 
}



void wheelsLeft ()      ///////
{
int pos1 = 70;    // variable to store the servo position    HOMBRO DCHO   FR1
int pos2 = 150;    // variable to store the servo position   HOMBRO IZDO    FL1
int pos3 = 42;    // variable to store the servo position    CADERA DCHA    BR1
int pos4 = 155;    // variable to store the servo position   CADERA IZDA    BL1
  
 FR1.write(pos1); 
 BR1.write(pos3); 
  while((currentMillis - previousMillis) < dPruebas)    //  dPruebas=interval=delay=retraso     ////    OJO  :: este While equivale a delay(dPruebas);
  { 
     currentMillis = millis();    // Se toma el tiempo actual
     
    //check sensors and respond if necessary 
  }

  previousMillis = currentMillis;
  currentMillis = millis();    // Se toma el tiempo actual 
}


void wheelsLeftSlow ()      ///////
{
int pos1 = 35;    // variable to store the servo position    HOMBRO DCHO   FR1
int pos2 = 130;    // variable to store the servo position   HOMBRO IZDO    FL1
int pos3 = 32;    // variable to store the servo position    CADERA DCHA    BR1
int pos4 = 130;    // variable to store the servo position   CADERA IZDA    BL1
  
 FR1.write(pos1); 
 BR1.write(pos3); 

  while((currentMillis - previousMillis) < dPruebas)    //  dPruebas=interval=delay=retraso     ////    OJO  :: este While equivale a delay(dPruebas);
  { 
     currentMillis = millis();    // Se toma el tiempo actual
     
    //check sensors and respond if necessary 
  }

  previousMillis = currentMillis;
  currentMillis = millis();    // Se toma el tiempo actual 
  FL1.write(pos2); 
  BL1.write(pos4); 

     while((currentMillis - previousMillis) < dPruebas)    //  dPruebas=interval=delay=retraso      ////    OJO  :: este While equivale a delay(dPruebas);
    { 
        currentMillis = millis();    // Se toma el tiempo actual
        
        //check sensors and respond if necessary 
    }
  previousMillis = currentMillis;
  currentMillis = millis();    // Se toma el tiempo actual 
}



void wheelsRight ()      ///////
{
int pos1 = 65;    // variable to store the servo position    HOMBRO DCHO   FR1
int pos2 = 160;    // variable to store the servo position   HOMBRO IZDO    FL1
int pos3 = 65;    // variable to store the servo position    CADERA DCHA    BR1
int pos4 = 165;    // variable to store the servo position   CADERA IZDA    BL1
  
 FL1.write(pos2); 
 BL1.write(pos4); 

  while((currentMillis - previousMillis) < dPruebas)    //  dPruebas=interval=delay=retraso     ////    OJO  :: este While equivale a delay(dPruebas);
  { 
     currentMillis = millis();    // Se toma el tiempo actual
     
    //check sensors and respond if necessary 
  }

  previousMillis = currentMillis;
  currentMillis = millis();    // Se toma el tiempo actual 
   FR1.write(pos1); 
   BR1.write(pos3); 

     while((currentMillis - previousMillis) < dPruebas)    //  dPruebas=interval=delay=retraso      ////    OJO  :: este While equivale a delay(dPruebas);
    { 
        currentMillis = millis();    // Se toma el tiempo actual
        
        //check sensors and respond if necessary 
    }
  previousMillis = currentMillis;
  currentMillis = millis();    // Se toma el tiempo actual 
}



void wheelsRightSlow ()      ///////
{
int pos1 = 60;    // variable to store the servo position    HOMBRO DCHO   FR1
int pos2 = 150;    // variable to store the servo position   HOMBRO IZDO    FL1
int pos3 = 58;    // variable to store the servo position    CADERA DCHA    BR1
int pos4 = 155;    // variable to store the servo position   CADERA IZDA    BL1
  
 FL1.write(pos2); 
 BL1.write(pos4); 

  while((currentMillis - previousMillis) < dPruebas)    //  dPruebas=interval=delay=retraso     ////    OJO  :: este While equivale a delay(dPruebas);
  { 
     currentMillis = millis();    // Se toma el tiempo actual
     
    //check sensors and respond if necessary 
  }

  previousMillis = currentMillis;
  currentMillis = millis();    // Se toma el tiempo actual 
   FR1.write(pos1); 
   BR1.write(pos3); 

     while((currentMillis - previousMillis) < dPruebas)    //  dPruebas=interval=delay=retraso      ////    OJO  :: este While equivale a delay(dPruebas);
    { 
        currentMillis = millis();    // Se toma el tiempo actual
        
        //check sensors and respond if necessary 
    }
  previousMillis = currentMillis;
  currentMillis = millis();    // Se toma el tiempo actual 
}


void wheelsBack ()      ///////FUNCION PARA QUE DE 1 PASO GIRANDO HACIA DELANTE solo con caderas
{
int pos1 = 140;    // variable to store the servo position    HOMBRO DCHO   FR1
int pos2 = 50;    // variable to store the servo position   HOMBRO IZDO    FL1
int pos3 = 140;    // variable to store the servo position    CADERA DCHA    BR1
int pos4 = 50;    // variable to store the servo position   CADERA IZDA    BL1
  
 FR1.write(pos1); 
 BR1.write(pos3); 
  while((currentMillis - previousMillis) < dPruebas)    //  dPruebas=interval=delay=retraso     ////    OJO  :: este While equivale a delay(dPruebas);
  { 
     currentMillis = millis();    // Se toma el tiempo actual
     
    //check sensors and respond if necessary 
  }
FL1.write(pos2);
BL1.write(pos4);

  previousMillis = currentMillis;
  currentMillis = millis();    // Se toma el tiempo actual
    previousMillis = currentMillis;
  currentMillis = millis();    // Se toma el tiempo actual

     while((currentMillis - previousMillis) < dPruebas)    //  dPruebas=interval=delay=retraso      ////    OJO  :: este While equivale a delay(dPruebas);
    { 
        currentMillis = millis();    // Se toma el tiempo actual
        
        //check sensors and respond if necessary 
    }
  previousMillis = currentMillis;
  currentMillis = millis();    // Se toma el tiempo actual 
}


void setSpeedMotors(int pos1, int pos2, int pos3, int pos4)      /////// pos1: hombro dcho FR1 ;  pos2: hombro izdo FL1 ;   pos3: cadera dcha BR1;  pos4:c adera izda BL1 
{
                                                               // Referencia adelante: int pos1 = 50; HOMBRO DCHO   FR1   int pos2 = 130;//    HOMBRO IZDO    FL1   // int pos3 = 50;   CADERA DCHA BR1 //  int pos4 = 130; CADERA IZDA    BL1

                                                                                          
 FR1.write(pos1); 
 BR1.write(pos3); 
  while((currentMillis - previousMillis) < dPruebas)    //  dPruebas=interval=delay=retraso     ////    OJO  :: este While equivale a delay(dPruebas);
  { 
     currentMillis = millis();    // Se toma el tiempo actual
     
    //check sensors and respond if necessary 
  }
FL1.write(pos2);
BL1.write(pos4);

  previousMillis = currentMillis;
  currentMillis = millis();    // Se toma el tiempo actual
    previousMillis = currentMillis;
  currentMillis = millis();    // Se toma el tiempo actual

     while((currentMillis - previousMillis) < dPruebas)    //  dPruebas=interval=delay=retraso      ////    OJO  :: este While equivale a delay(dPruebas);
    { 
        currentMillis = millis();    // Se toma el tiempo actual
        
        //check sensors and respond if necessary 
    }
  previousMillis = currentMillis;
  currentMillis = millis();    // Se toma el tiempo actual 
}

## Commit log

2020-05-19 Add files via upload
    Arduino code for gamaker-bot Crawler
2020-05-21 Add files via upload
    Soporte para un sensor ultrasónico y 3 leds
    [soportesensorUS_Final.stl]
2020-05-23 Add files via upload
    Test to check the speed of your 360 º servos
